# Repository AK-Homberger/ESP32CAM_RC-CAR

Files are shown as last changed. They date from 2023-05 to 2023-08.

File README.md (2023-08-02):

# ESP32-CAM RC Car

This repository shows how to build a WLAN controlled RC Car with an ESP32-CAM.
With a web interface you can control the car and the camera view is shown in the browser. 

It is possible to move the camera up and down with a small servo attached to the housing. Here is a small [Video](https://www.dropbox.com/s/yz9jac4miu72km5/IMG_2094.MOV?dl=0).

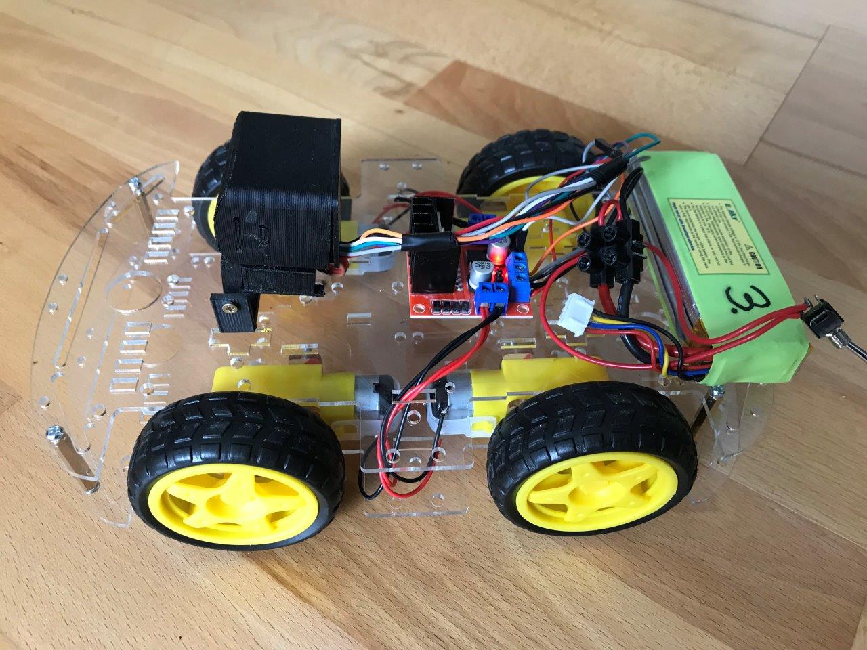
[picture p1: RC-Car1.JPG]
RC-Car1


## Hardware
All necessary parts are listed below in the parts section with links to order. 

As chassis, I use the Joy-IT ROBOT CAR KIT 01. This is easy to mount. Just follow the assembling instructions.

On the chassis, you can screw the camera to the top plate using one of the pre-drilled holes. The motor driver and the battery, I simply connected with double sided tape.

The two motors left and right are connected (soldered) in [parallel](Motor.jpg). Make sure that they move in the same direction when powered. As motor driver the L298N is used. The left/right motor is the connected to the two outputs on the motor driver. Make sure that direction is right for forward/backwards for both sides. If necessary change the cable connection. 

The motor driver is also providing the 5 Volt for the ESP32CAM. The power supply for the servo is done with an extra 7805 voltage regulator. This was necessary due to stability problems, if ESP and Servo is supplied directly from the motor driver.

The ESP32CAM is located in a 3D printed housing. The files are available on [Thingiverse](https://www.thingiverse.com/thing:3579507). For mounting the housing to chassis you can either use the round bottom plate from Thingiverse or you can use my [mount](ESP32-CAM_Mount2.stl) instead. The servo arm has to be connected with bottom part with [metal wire](Servo.JPG). For the lenght of the connection wire you have to try a bit. For me, 20 mm worked well.

The 9g Micro Servo have to be placed and screwed into the 3D housing.

The components have to be connected as shown in the diagram. I'm using 20 cm [jumper wires](https://www.reichelt.de/entwicklerboards-steckbrueckenkabel-20cm-3x-20-kabel-debo-kabelset8-p280591.html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) for the connection.

As battery you can use anything between 7.4 to 11.1 Volt. I'm using a 11.1 Volt lithium polymer accu from a RC helicopter.

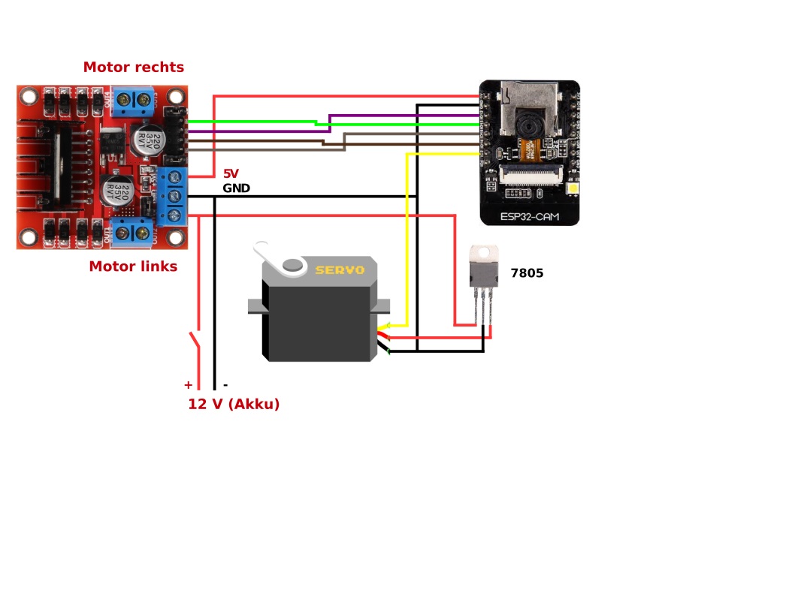
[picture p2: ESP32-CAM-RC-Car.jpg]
Wiring


## Software
The RC Car Code is prepared for the Arduino IDE. To install the sketch, download the whole repository and then open the file "ESP32CAM-RC-Car.ino" in the IDE. Then edit the code to adjust the WLAN credentials according to your local needs. That's it. As board please select the "AI Thinker ESP32-CAM" or "ESP32 Wrover Module" in the Arduino IDE. And please make sure you have the ESP32 board URL provided in the preferences (https://raw.githubusercontent.com/espressif/arduino-esp32/gh-pages/package_esp32_index.json). And select board version 1.0.6. Otherwise you will get compile errors regarding missing header files.

You need an external (FTDI) programmer to install the (initial) sketch on the ESP32-CAM module. You have to set the voltage of the adapter to 5 Volt.

FTDI

For programming you have to connect IO0 to GND, RX/TX (crossed) and 5V/GND. If you have the power supply already connected, then do not connect the 5V cable from the adapter. Then press the "RST" button on the ESP32-CAM. After that, you can start the upload process within the Arduino IDE (with FTDI USB-Serial port selected). For normal start open IO0 from GND and press "RST" again. 

After initial programming you can do uploads via OTA. Device name is "RC-Car".

## Web Control
The RC car can be controlled with a small web interface. Just power the car. The ESPCAM LED is flashing 5 times.

If your client is supporting MDNS, then you can simply enter "rc-car.local" in the address field. Otherwise you have to provide the IP-Address (shown in Serial Monitor after programming).

To start the stream, just press the "Start Stream" button. You can move forward/backward and left/right. With "Flash" you can set the power of the internal LED. With "Speed" you can adjust the speed of the car. With "Servo" you can move the camera view up and down. With "Quality/Resolution" you can define the camera settings for both options. With "Get Still" you can take a picture.

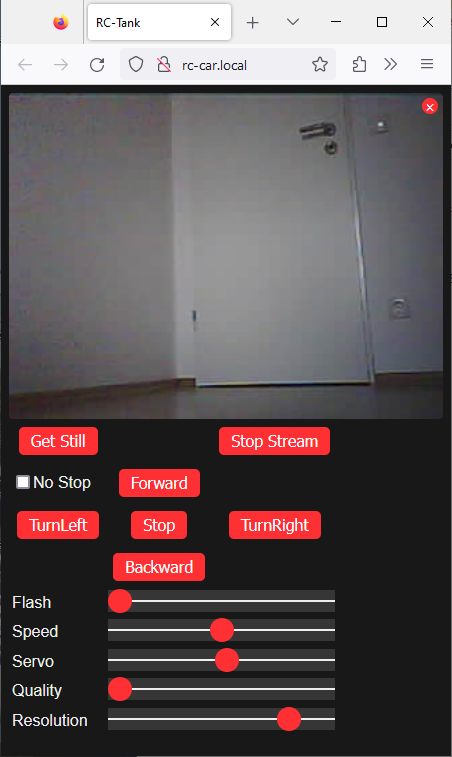
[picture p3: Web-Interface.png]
Interface


## ESP32CAM pinout


# Parts
- ESP32-CAM [Link](https://www.reichelt.de/entwicklerboards-esp32-kamera-2mp-25--debo-cam-esp32-p266036.html?&nbc=1)
- Car Kit [Link](https://www.reichelt.de/roboter-fahrgestell-kit-fuer-alle-arduino-systeme-robot-car-kit-01-p219024.html?&nbc=1)
- Motor Driver [Link](https://www.reichelt.de/entwicklerboards-motodriver2-l298n-debo-motodriver2-p202829.html?&nbc=1)
- Servo [Link](https://www.reichelt.de/servo-high-end-micro-analog-jamara-033212-p238316.html?&nbc=1)
- 7805 [Link](https://www.reichelt.de/festspannungsregler-5-v-1-5-a-to-220-3-ua-7805-ckcs-p189073.html?&nbc=1)
- Switch [Link](https://www.reichelt.de/miniatur-kippschalter-ein-aus-ein-3-a-250-v-goobay-10022-p285989.html?&nbc=1)
- Accu [Link](https://www.reichelt.de/akku-pack-li-polymer-7-4-v-900-mah-rd-xt-900-s2-p336955.html?&nbc=1)
- Cable [Link](https://www.reichelt.de/entwicklerboards-steckbrueckenkabel-20cm-3x-20-kabel-debo-kabelset8-p280591.html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)
- USB to Serial Adapter [Link1](https://www.reichelt.de/entwicklerboards-microusb-buchse-auf-uart-ft232-debo-musb2uart-3-p266053.html?&nbc=1) or [Link2](https://www.amazon.de/dp/B07R17BMTL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)
- 3D Print Camera Mount [Link](https://www.thingiverse.com/thing:3579507)

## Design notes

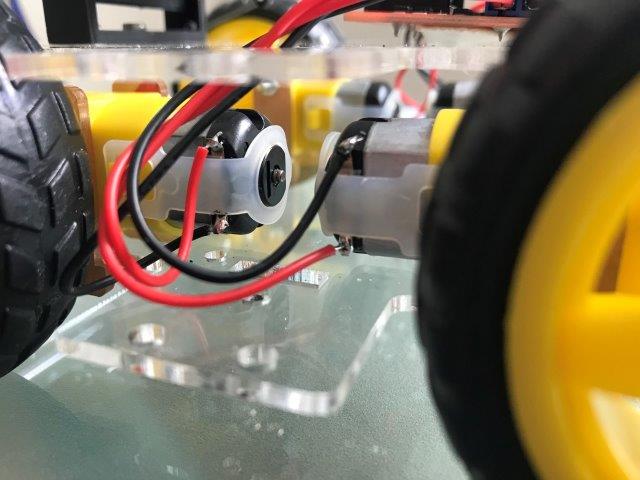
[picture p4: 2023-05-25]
Motor.jpg

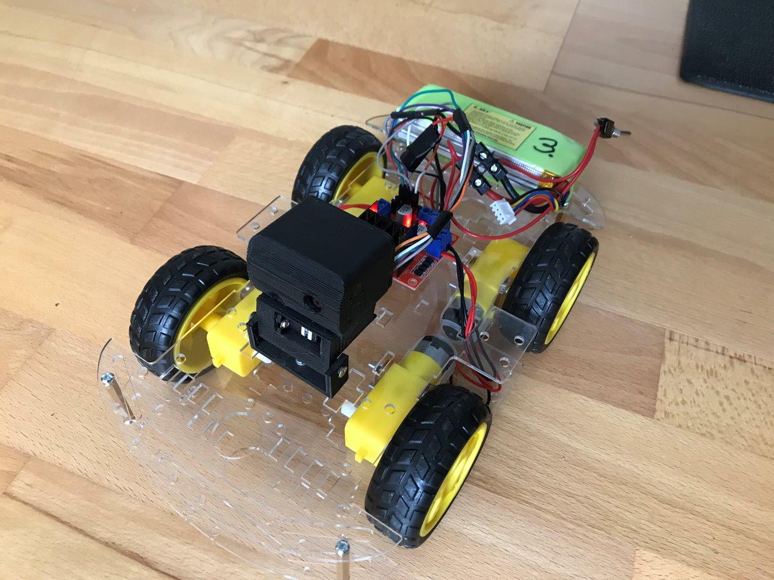
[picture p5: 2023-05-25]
RC-Car2.JPG

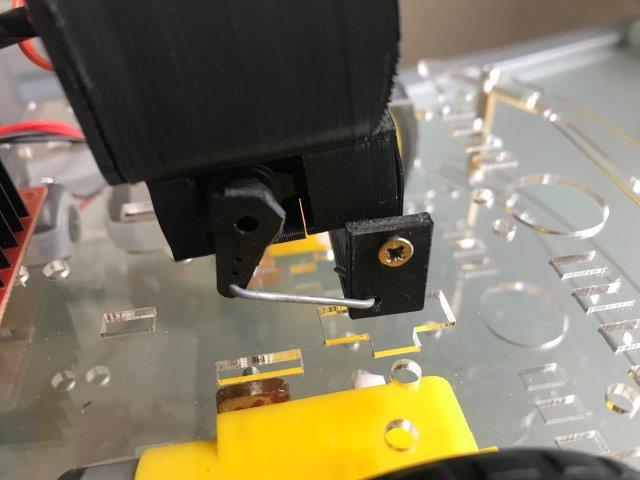
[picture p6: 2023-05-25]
Servo.JPG

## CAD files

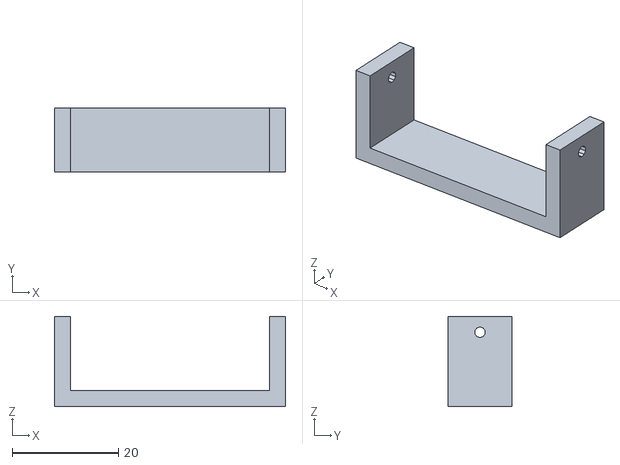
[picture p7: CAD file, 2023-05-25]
ESP32-CAM_Mount2.stl
43.5 x 12.0 x 17.0

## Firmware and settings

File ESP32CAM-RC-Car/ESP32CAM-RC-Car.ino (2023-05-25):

/*
  This code is free software; you can redistribute it and/or
  modify it under the terms of the GNU Lesser General Public
  License as published by the Free Software Foundation; either
  version 2.1 of the License, or (at your option) any later version.
  This code is distributed in the hope that it will be useful,
  but WITHOUT ANY WARRANTY; without even the implied warranty of
  MERCHANTABILITY or FITNESS FOR A PARTICULAR PURPOSE.  See the GNU
  Lesser General Public License for more details.
  You should have received a copy of the GNU Lesser General Public
  License along with this library; if not, write to the Free Software
  Foundation, Inc., 51 Franklin St, Fifth Floor, Boston, MA  02110-1301  USA
*/

// ESP32-CAM Remote Controlled Car

// Just change the WLAN credential to use it!!
// No additional libraries have to be installed for this project
// Make sure you have selected ESP32 Wrover Module in Arduino IDE

#include <esp_wifi.h>
#include <esp_camera.h>
#include <WiFi.h>
#include <ESPmDNS.h>
#include <WiFiUdp.h>
#include <soc/soc.h>
#include <soc/rtc_cntl_reg.h>
#include <ArduinoOTA.h>

// Select camera model
#define CAMERA_MODEL_AI_THINKER

#define PWDN_GPIO_NUM     32
#define RESET_GPIO_NUM    -1
#define XCLK_GPIO_NUM      0
#define SIOD_GPIO_NUM     26
#define SIOC_GPIO_NUM     27

#define Y9_GPIO_NUM       35
#define Y8_GPIO_NUM       34
#define Y7_GPIO_NUM       39
#define Y6_GPIO_NUM       36
#define Y5_GPIO_NUM       21
#define Y4_GPIO_NUM       19
#define Y3_GPIO_NUM       18
#define Y2_GPIO_NUM        5
#define VSYNC_GPIO_NUM    25
#define HREF_GPIO_NUM     23
#define PCLK_GPIO_NUM     22

// Change WLAN credentials according to your local settings
const char* ssid = "ssid";
const char* password = "password";

// Pin definitions for both motors and servo
const int MotPin0 = 15;  // Left +
const int MotPin1 = 14;  // Left -
const int MotPin2 = 13;  // Right -
const int MotPin3 = 12;  // Right +
const int ServoPin = 2;  // Pin for camera up/down servo

void startCameraServer();// Forward declaration of function


//*****************************************************************************
void setup() {
  WRITE_PERI_REG(RTC_CNTL_BROWN_OUT_REG, 0); // prevent brownouts by silencing them

  Serial.begin(115200);
  Serial.setDebugOutput(true);
  Serial.println();

  camera_config_t config;
  config.ledc_channel = LEDC_CHANNEL_0;
  config.ledc_timer = LEDC_TIMER_0;
  config.pin_d0 = Y2_GPIO_NUM;
  config.pin_d1 = Y3_GPIO_NUM;
  config.pin_d2 = Y4_GPIO_NUM;
  config.pin_d3 = Y5_GPIO_NUM;
  config.pin_d4 = Y6_GPIO_NUM;
  config.pin_d5 = Y7_GPIO_NUM;
  config.pin_d6 = Y8_GPIO_NUM;
  config.pin_d7 = Y9_GPIO_NUM;
  config.pin_xclk = XCLK_GPIO_NUM;
  config.pin_pclk = PCLK_GPIO_NUM;
  config.pin_vsync = VSYNC_GPIO_NUM;
  config.pin_href = HREF_GPIO_NUM;
  config.pin_sscb_sda = SIOD_GPIO_NUM;
  config.pin_sscb_scl = SIOC_GPIO_NUM;
  config.pin_pwdn = PWDN_GPIO_NUM;
  config.pin_reset = RESET_GPIO_NUM;
  config.xclk_freq_hz = 20000000;
  config.pixel_format = PIXFORMAT_JPEG;
  
  // Init with high specs to pre-allocate larger buffers
  if (psramFound()) {
    config.frame_size = FRAMESIZE_QVGA;
    config.jpeg_quality = 10;
    config.fb_count = 2;
  } else {
    config.frame_size = FRAMESIZE_QVGA;
    config.jpeg_quality = 12;
    config.fb_count = 1;
  }

  // Camera init
  esp_err_t err = esp_camera_init(&config);
  if (err != ESP_OK) {
    Serial.printf("Camera init failed with error 0x%x", err);
    return;
  }

  // Drop down frame size for higher initial frame rate
  sensor_t * s = esp_camera_sensor_get();
  s->set_framesize(s, FRAMESIZE_QVGA);
  s->set_vflip(s, 0);
  s->set_hmirror(s, 0);

  // Init Remote Control Car
  initMotors();
  initServo();

  ledcSetup(7, 5000, 8);
  ledcAttachPin(4, 7);  // pin4 is LED
  
  // Init WiFi
  WiFi.mode(WIFI_STA);
  WiFi.setHostname("RC-Car");
  WiFi.begin(ssid, password);
  delay(500);

  long int StartTime = millis();
  while (WiFi.status() != WL_CONNECTED)
  {
    delay(500);
    if ((StartTime + 10000) < millis()) break;
  }

  /*
    int8_t power;
    esp_wifi_set_max_tx_power(20);
    esp_wifi_get_max_tx_power(&power);
    Serial.printf("wifi power: %d \n",power);
  */

  startCameraServer();

  if (WiFi.status() == WL_CONNECTED)
  {
    Serial.println("");
    Serial.println("WiFi connected");
    Serial.print("Camera Ready! Use 'http://");
    Serial.print(WiFi.localIP());
    Serial.println("' to connect");
  } else {
    Serial.println("");
    Serial.println("WiFi disconnected");
    Serial.print("Camera Ready! Use 'http://");
    Serial.print(WiFi.softAPIP());    // Start Access Point
    Serial.println("' to connect");
    char* apssid = "ESP32-Car";
    char* appassword = "12345678";         // AP password require at least 8 characters.
    WiFi.softAP((WiFi.softAPIP().toString() + "_" + (String)apssid).c_str(), appassword);
  }

  for (int i = 0; i < 5; i++)
  {
    ledcWrite(7, 10); // flash led
    delay(200);
    ledcWrite(7, 0);
    delay(200);
  }

  // Arduino OTA config and start
  ArduinoOTA.setHostname("RC-Car");
  ArduinoOTA.begin();

  // Arduino MDNS config and start
  MDNS.begin("RC-Car");
  MDNS.addService("http", "tcp", 80);
}


//*****************************************************************************
// Initialise the motors
// Define pulse width modulation channels and attach to defined motor pins

void initMotors()
{
  ledcSetup(3, 2000, 8); // 2000 hz PWM, 8-bit resolution
  ledcSetup(4, 2000, 8); // 2000 hz PWM, 8-bit resolution
  ledcSetup(5, 2000, 8); // 2000 hz PWM, 8-bit resolution
  ledcSetup(6, 2000, 8); // 2000 hz PWM, 8-bit resolution
  ledcAttachPin(MotPin0, 3); // Left +
  ledcAttachPin(MotPin1, 4); // left -
  ledcAttachPin(MotPin2, 5); // Right -
  ledcAttachPin(MotPin3, 6); // Right +
}


//*****************************************************************************
// Initialise the servo
// Define pulse width modulation channel and attach to defined servo pin

void initServo()
{
  ledcSetup(8, 50, 16); // 50 hz PWM, 16-bit resolution, range from 3250 to 6500.
  ledcAttachPin(ServoPin, 8);
  ledcWrite(8, 10 * 520);
}


//*****************************************************************************
void loop() {
  ArduinoOTA.handle();
}

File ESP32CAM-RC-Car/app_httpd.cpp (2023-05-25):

#include <esp32-hal-ledc.h>
#include "esp_http_server.h"
#include "esp_timer.h"
#include "esp_camera.h"
#include "img_converters.h"
#include "Arduino.h"

//#include "dl_lib.h"
#include "fb_gfx.h"
#include "fd_forward.h"
#include "fr_forward.h"

int speed = 128;
int noStop = 0;


typedef struct {
  httpd_req_t *req;
  size_t len;
} jpg_chunking_t;

#define PART_BOUNDARY "123456789000000000000987654321"
static const char* _STREAM_CONTENT_TYPE = "multipart/x-mixed-replace;boundary=" PART_BOUNDARY;
static const char* _STREAM_BOUNDARY = "\r\n--" PART_BOUNDARY "\r\n";
static const char* _STREAM_PART = "Content-Type: image/jpeg\r\nContent-Length: %u\r\n\r\n";

httpd_handle_t stream_httpd = NULL;
httpd_handle_t camera_httpd = NULL;

static size_t jpg_encode_stream(void * arg, size_t index, const void* data, size_t len) {
  jpg_chunking_t *j = (jpg_chunking_t *)arg;
  if (!index) {
    j->len = 0;
  }
  if (httpd_resp_send_chunk(j->req, (const char *)data, len) != ESP_OK) {
    return 0;
  }
  j->len += len;
  return len;
}

static esp_err_t capture_handler(httpd_req_t *req) {
  camera_fb_t * fb = NULL;
  esp_err_t res = ESP_OK;
  int64_t fr_start = esp_timer_get_time();

  fb = esp_camera_fb_get();
  if (!fb) {
    Serial.println("Camera capture failed");
    httpd_resp_send_500(req);
    return ESP_FAIL;
  }

  httpd_resp_set_type(req, "image/jpeg");
  httpd_resp_set_hdr(req, "Content-Disposition", "inline; filename=capture.jpg");

  size_t out_len, out_width, out_height;
  uint8_t * out_buf;
  bool s;
  {
    size_t fb_len = 0;
    if (fb->format == PIXFORMAT_JPEG) {
      fb_len = fb->len;
      res = httpd_resp_send(req, (const char *)fb->buf, fb->len);
    } else {
      jpg_chunking_t jchunk = {req, 0};
      res = frame2jpg_cb(fb, 80, jpg_encode_stream, &jchunk) ? ESP_OK : ESP_FAIL;
      httpd_resp_send_chunk(req, NULL, 0);
      fb_len = jchunk.len;
    }
    esp_camera_fb_return(fb);
    int64_t fr_end = esp_timer_get_time();
    Serial.printf("JPG: %uB %ums\n", (uint32_t)(fb_len), (uint32_t)((fr_end - fr_start) / 1000));
    return res;
  }

  dl_matrix3du_t *image_matrix = dl_matrix3du_alloc(1, fb->width, fb->height, 3);
  if (!image_matrix) {
    esp_camera_fb_return(fb);
    Serial.println("dl_matrix3du_alloc failed");
    httpd_resp_send_500(req);
    return ESP_FAIL;
  }

  out_buf = image_matrix->item;
  out_len = fb->width * fb->height * 3;
  out_width = fb->width;
  out_height = fb->height;

  s = fmt2rgb888(fb->buf, fb->len, fb->format, out_buf);
  esp_camera_fb_return(fb);
  if (!s) {
    dl_matrix3du_free(image_matrix);
    Serial.println("to rgb888 failed");
    httpd_resp_send_500(req);
    return ESP_FAIL;
  }

  jpg_chunking_t jchunk = {req, 0};
  s = fmt2jpg_cb(out_buf, out_len, out_width, out_height, PIXFORMAT_RGB888, 90, jpg_encode_stream, &jchunk);
  dl_matrix3du_free(image_matrix);
  if (!s) {
    Serial.println("JPEG compression failed");
    return ESP_FAIL;
  }

  int64_t fr_end = esp_timer_get_time();
  return res;
}

static esp_err_t stream_handler(httpd_req_t *req) {
  camera_fb_t * fb = NULL;
  esp_err_t res = ESP_OK;
  size_t _jpg_buf_len = 0;
  uint8_t * _jpg_buf = NULL;
  char * part_buf[64];
  dl_matrix3du_t *image_matrix = NULL;

  static int64_t last_frame = 0;
  if (!last_frame) {
    last_frame = esp_timer_get_time();
  }

  res = httpd_resp_set_type(req, _STREAM_CONTENT_TYPE);
  if (res != ESP_OK) {
    return res;
  }

  while (true) {
    fb = esp_camera_fb_get();
    if (!fb) {
      Serial.println("Camera capture failed");
      res = ESP_FAIL;
    } else {
      {
        if (fb->format != PIXFORMAT_JPEG) {
          bool jpeg_converted = frame2jpg(fb, 80, &_jpg_buf, &_jpg_buf_len);
          esp_camera_fb_return(fb);
          fb = NULL;
          if (!jpeg_converted) {
            Serial.println("JPEG compression failed");
            res = ESP_FAIL;
          }
        } else {
          _jpg_buf_len = fb->len;
          _jpg_buf = fb->buf;
        }
      }
    }
    if (res == ESP_OK) {
      size_t hlen = snprintf((char *)part_buf, 64, _STREAM_PART, _jpg_buf_len);
      res = httpd_resp_send_chunk(req, (const char *)part_buf, hlen);
    }
    if (res == ESP_OK) {
      res = httpd_resp_send_chunk(req, (const char *)_jpg_buf, _jpg_buf_len);
    }
    if (res == ESP_OK) {
      res = httpd_resp_send_chunk(req, _STREAM_BOUNDARY, strlen(_STREAM_BOUNDARY));
    }
    if (fb) {
      esp_camera_fb_return(fb);
      fb = NULL;
      _jpg_buf = NULL;
    } else if (_jpg_buf) {
      free(_jpg_buf);
      _jpg_buf = NULL;
    }
    if (res != ESP_OK) {
      break;
    }
    int64_t fr_end = esp_timer_get_time();
    int64_t frame_time = fr_end - last_frame;
    last_frame = fr_end;
    frame_time /= 1000;
    Serial.printf("MJPG: %uB %ums (%.1ffps)\n",
                  (uint32_t)(_jpg_buf_len),
                  (uint32_t)frame_time, 1000.0 / (uint32_t)frame_time
                 );
  }

  last_frame = 0;
  return res;
}

enum state {fwd, rev, stp};
state actstate = stp;
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
